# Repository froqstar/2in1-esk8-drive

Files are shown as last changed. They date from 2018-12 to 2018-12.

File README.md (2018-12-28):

# 2in1-esk8-drive
A parametric 3D design for single-motor, dual driven wheel electric skateboards

## What is this about?

This is a parametric 3D design for a electric skateboard motor mount. 
The feature that sets it apart is that it allows to use one motor to drive two wheels of a skateboard, 
giving it more traction especially in cornering.

The parts generated by the OpenSCAD script are shown below:
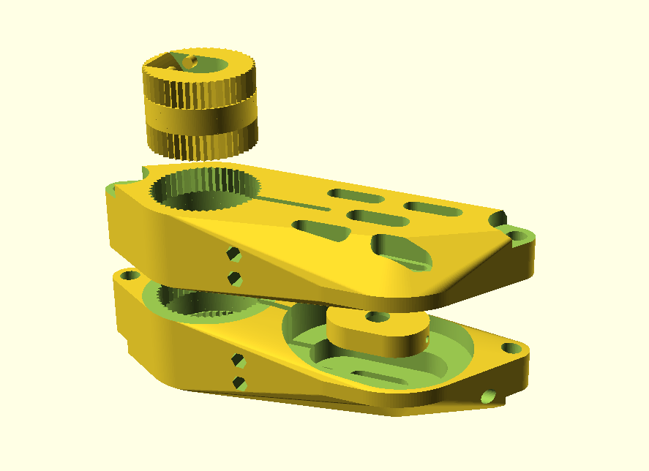
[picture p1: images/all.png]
The whole thing


## Features

- Dual wheel drive with one brushless DC motor/ESC
- Completely parametric, adjustable to your existing hardware
- Vibration-dampened (the parts touching the truck are expected to be printed in TPU)
- Variable mount-to-truck angle
- Belt-tensioning via setscrew

## How do I make this work for my board?

As the design is parametric, almost all parameters can be adjusted according to your setup.
This includes truck and motor dimensions, as well as the type and length of belt used, the number of teeth on your 
pulleys, the diameters of your screws and how sturdy you want the design to be. So just about everything.

The only thing probably requiring some work on your side is the TPU adapter to make it fit to your truck.
Due to the plethora of truck shapes out there and me only having my single board, 
I couldn't model them myself. By default, an adapter for Globe Slant Reverse Kingpin Trucks is included.
Take the output of `truckAdapterBase()` as a base for your own truck adapter.

## Hardware BOM

- A suitable BLDC motor (The current script has the values for a Turnigy Aerodrive SK3 6474 motor)
- Mounting screws for the motor (should be included)
- Two drive belts (HTD5M or similar, 12mm width or more recommended)
- Two wheel & two motor pulleys, fitting your belts.
- A new axle for your motor! As most motors don't support pulleys on both sides, you'll likely need to replace the motor axle with a longer one that protrudes from both ends of the motor. I made one myself.
- 4 screws and locknuts of suitable length and strength (e.g. M3 40mm) to fasten the big parts around the TPU parts.
- 1 screw and locknut to adjust the belt tension on the non-supported motor side. M3 is fine, length depends on the rest of your hardware/parameters.
- 1 bearing for the motor axle. If your motor axle is 8mm in diameter, a standard 608 skateboard bearing is fine.
- Two pieces of threaded rod (e.g. M8) as long as your truck axle is wide, with 8 matching nuts (preferably locknuts) to adjust the distance between the two sides of the mount.  

## Assembly

### Printing the parts
Once you have put in your measurements, all you need to do is open the supplied .scad file with OpenSCAD, generate the STL files and print them.
All parts are expected to be printed in PETG or similar (PLA is not recommended due to it being brittle and having low tolerance for motor heat), except for the truck adapter (the round thing), which is expected to be printed in TPU to make it pressure-fit tightly on the truck and offer vibration dampening for the whole assembly.
Print one of each PETG part, and two TPU truck adapters.

### Steps

1. Slip the truck adapters on your truck.
2. Loosely attach the motor to the mount through the 4 mounting holes.
3. Put in the screws and nuts that are used to fasten the mount around the adapters. Don't tighten them yet, or you won't be able to attach the parts to the truck!
4. Slip the motor mount over the truck adapter in the desired angle and make sure the mount doesn't touch your board when cornering.
5. Put the motor axle bearing in the bearing sleigh, and insert the locknut in the slot. Then, put the bearing sleigh into the cavity in the mount part, bearing-first and with the locknut facing the hole for the tensioning screw. Screw the tensioning screw into the nut.
6. Slip the mount on the other truck adapter on the truck and fit the motor axle in the bearing.
7. Put the threaded rods through the holes at the front and the back parts of the mount, making sure not to forget to put on the two nuts in the middle.
8. Adjust the distance between the mounts.
9. Fasten the mounts around the truck adapters by tightening the four screws.
10. Put on your pulleys, wheels and belts and tension accordingly.
11. Profit :)

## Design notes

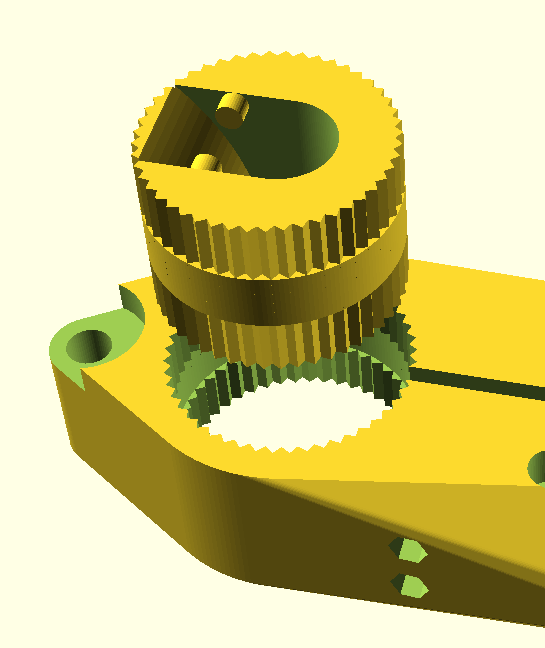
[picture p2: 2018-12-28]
images/adapter.png

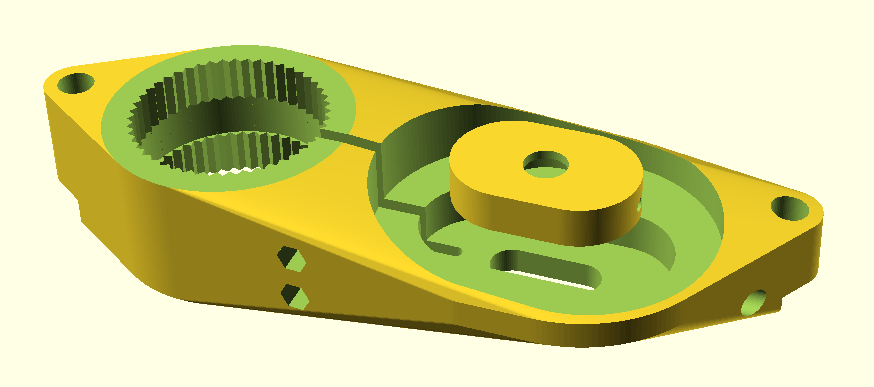
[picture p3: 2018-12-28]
images/bearing.png

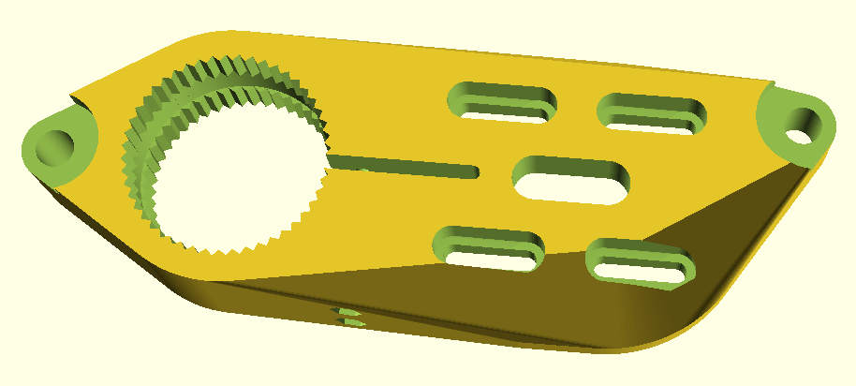
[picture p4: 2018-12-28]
images/motor.png

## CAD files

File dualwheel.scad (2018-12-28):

$fa=2;
$fs=0.4;

PI = 3.14159;

//all values are in mm


// Truck parameters
useableTruckSize = 154; // The distance between the wheels (measured from rubber to rubber, NOT bearing to bearing!)
truckWidth = 18;
truckAdapterDiameter = 42; // You may need to increase this when you have a very thick truck
truckAdapterPlay = 1.3;
truckAdapterAdjustmentAngle = 7.5; // stepsize of mount-to-truck angle adjustment. Has to be a clean divisor of 90°. Smaller steps are harder to print/have less strength!
truckAdapterTensioningSlotWidth = 3; 
truckAdapterTensioningSlotLength = 30;
truckAdapterTensioningScrewDiameter = 3.1;
truckAdapterTensioningScrewLength = 30;
truckAdapterTensioningScrewCount = 2;
truckAdapterTensioningScrewHeadDiameter = 6.1;
truckAdapterTensioningScrewNutDiameter = 5.7;

distanceScrewDiameter = 8; // The screws used to keep the two mounts at constant distance, at motor & axis

// Transmission parameters
beltWidth = 15;
beltLength = 280;
motorPulleyTeeth = 15;
wheelPulleyTeeth = 40;
wheelPulleyWidth = 19;
beltPitch = 5;

motorPulleyCircumference = motorPulleyTeeth * beltPitch;
wheelPulleyCircumference = wheelPulleyTeeth * beltPitch;

// Motor parameters
// SK3 6374 values: http://www.electric-skateboard.builders/uploads/db1493/original/3X/c/4/c40213f09c3a9efb59e033c84dde2ed19bf27e4f.png
motorHousingDiameter = 59; //59
motorHousingDepth = 84.5;
motorClearing = 2;
motorAxisDiameter = 8;
motorAxisClearing = 0.7;
motorClipDiameter = 15;
motorClipDepth = 2;
motorScrewHoleCount = 4;
motorScrewHoleDiameter = 4.4;
motorScrewHoleSpacing = 44;
motorScrewHoleTensioningSpan = 15;
motorScrewHeadDiameter = 8;

// Motor axis bearing parameters
bearingDiameter = 22.1;
bearingDepth = 7;
bearingWallWidth = 2;
bearingScrewDiameter = 3;
bearingScrewNutDiameter = 5.7;
bearingScrewNutHeight = 4.4;
bearingScrewHeadDiameter = 6;

// General structural parameters
truckMountWidth = 30; // width of the truck side of the mount
motorMountWidth = (useableTruckSize - 2 - wheelPulleyWidth*2 - motorHousingDepth) / 2; // width of the motor side of the mount
wallWidth = 6; // the minimum wall width of parts

// The distance between the wheel axis and the motor axis (midpoints).
// Yes, this is incorrect, but that is what the tensioning holes are for ;)
axesDistance = (beltLength - motorPulleyCircumference/2 - wheelPulleyCircumference/2) / 2;


module motorMount() {
	difference() {
		//create outer hull
		mountHullWithAxisHole(false);
		
		//motor clip clearing
		hull() {
			translate([axesDistance - motorScrewHoleTensioningSpan/2, 0, motorMountWidth - motorClipDepth]) {
				cylinder(h=motorClipDepth, d = motorClipDiameter);
			}
			translate([axesDistance + motorScrewHoleTensioningSpan/2, 0, motorMountWidth - motorClipDepth]) {
				cylinder(h=motorClipDepth, d = motorClipDiameter);
			}
		}
		
		//motor mount holes
		for (i = [0:motorScrewHoleCount]) {
			hull() {
				translate([axesDistance - motorScrewHoleTensioningSpan/2, 0, 0]) {
					motorMountingHole(i);
				}
				translate([axesDistance + motorScrewHoleTensioningSpan/2, 0, 0]) {
					motorMountingHole(i);
				}
			}
			hull() {
				translate([axesDistance - motorScrewHoleTensioningSpan/2, 0, -0.5]) { //do a slight slope for the screw head to keep it from sliding inwards
					motorMountingScrewHead(i);
				}
				translate([axesDistance + motorScrewHoleTensioningSpan/2, 0, 0]) {
					motorMountingScrewHead(i);
				}
			}
		}
	}
}

module bearingMount() {
	difference() {
		//create outer hull
		mountHullWithAxisHole(true);
		
		//pocket for bearing sleigh
		translate([axesDistance, 0, motorMountWidth - bearingDepth - bearingWallWidth]) {
			hull() {
				translate([-motorScrewHoleTensioningSpan/2, 0, 0]) {
					bearingSleigh();
				}
				translate([+motorScrewHoleTensioningSpan/2, 0, 0]) {
					bearingSleigh();
				}
			}
			//setscrew
			translate([bearingDiameter/2, 0, bearingDepth/2]) {
				rotate([0,90,0]) {
					cylinder(h=bearingWallWidth + wallWidth + 30, d=bearingScrewDiameter);
				}
			}
			//setscrew head hole
			translate([motorScrewHoleTensioningSpan/2 + bearingDiameter + wallWidth, 0, bearingDepth/2]) {
				rotate([0,90,0]) {
					cylinder(h=wallWidth + 30, d=bearingScrewHeadDiameter);
				}
			}
		}
	}
}


module mountHullWithAxisHole(isLeft = false) {
	difference() {
		//outer shape
		hull() {
			cylinder(h=truckMountWidth, r=truckAdapterDiameter/2 + wallWidth);
			
			translate([axesDistance - motorScrewHoleTensioningSpan/2, 0, 0]) {
				hull() {
					cylinder(h=wallWidth, r=motorPulleyCircumference/(2*PI) + 2);
					translate([0,0,motorMountWidth]) {
						cylinder(h=wallWidth, r=motorHousingDiameter/2 + motorClearing);
					}
				}
			}
			translate([axesDistance + motorScrewHoleTensioningSpan/2, 0, 0]) {
				hull() {
					cylinder(h=wallWidth, r=motorPulleyCircumference/(2*PI) + 2);
					translate([0,0,motorMountWidth]) {
						cylinder(h=wallWidth, r=motorHousingDiameter/2 + motorClearing);
					}
				}
			}
			// rear distance screw mount
			translate([-(truckAdapterDiameter/2+wallWidth*2+distanceScrewDiameter/2), 0, 0]) {
				cylinder(h=truckMountWidth, d=distanceScrewDiameter+wallWidth);
			}
			// front distance screw mount
			translate([axesDistance + motorHousingDiameter/2 + wallWidth*3, (isLeft ? 1:-1) * (motorHousingDiameter/2 - wallWidth*2), 0]) {
				cylinder(h=motorMountWidth + wallWidth, d=distanceScrewDiameter+wallWidth);
			}
		}
		// rear distance screw hole
		translate([-(truckAdapterDiameter/2+wallWidth*2+distanceScrewDiameter/2), 0, 0]) {
			cylinder(h=truckMountWidth, d=distanceScrewDiameter);
		}
		translate([-(truckAdapterDiameter/2+wallWidth*2+distanceScrewDiameter/2), 0, 0]) {
			cylinder(d=21, h=6);
		}
		// front distance screw hole
		translate([axesDistance + motorHousingDiameter/2 + wallWidth*3, (isLeft ? 1:-1) * (motorHousingDiameter/2 - wallWidth*2), 0]) {
			cylinder(h=truckMountWidth, d=distanceScrewDiameter);
		}
		translate([axesDistance + motorHousingDiameter/2 + wallWidth*3, (isLeft ? 1:-1) * (motorHousingDiameter/2 - wallWidth*2), 0]) {
			cylinder(d=21, h=6);
		}
		
		//axis hole
		hull() {
			translate([axesDistance - motorScrewHoleTensioningSpan/2, 0, 0]) {
				cylinder(h=motorMountWidth, r = motorAxisDiameter/2 + motorAxisClearing);
			}
			translate([axesDistance + motorScrewHoleTensioningSpan/2, 0, 0]) {
				cylinder(h=motorMountWidth, r = motorAxisDiameter/2 + motorAxisClearing);
			}
		}
		//plain mount surfaces
		translate([0,0,truckMountWidth]) {
			cylinder(h=motorMountWidth, d=truckAdapterDiameter + 2*wallWidth);
		}
		hull() {
			translate([axesDistance - motorScrewHoleTensioningSpan/2, 0, motorMountWidth]) {
				cylinder(h=motorMountWidth, r = motorHousingDiameter/2);
			}
			translate([axesDistance + motorScrewHoleTensioningSpan/2, 0, motorMountWidth]) {
				cylinder(h=motorMountWidth, r = motorHousingDiameter/2);
			}
		}
		
		truckAdapterBase(truckAdapterDiameter + truckAdapterPlay);
		
		//truck adapter tensioning slot
		hull() {
			cylinder(h=truckMountWidth, d=truckAdapterTensioningSlotWidth);
			translate([truckAdapterDiameter/2 + truckAdapterTensioningSlotLength,0,0]) {
				cylinder(h=truckMountWidth, d=truckAdapterTensioningSlotWidth);
			}
		}
		//truck adapter tensioner screwholes
		for (i = [0:truckAdapterTensioningScrewCount-1]) {
			truckSlotTensioningScrewHole(i, isLeft);
		}
	}
}


module motorMountingHole(number) {
	rotate([0,0,360/motorScrewHoleCount*number + (360/motorScrewHoleCount)/2]) {
		translate([motorScrewHoleSpacing/2,0,0]) {
			cylinder(h=motorMountWidth, d=motorScrewHoleDiameter);
		}
	}
}

module motorMountingScrewHead(number) {
	rotate([0,0,360/motorScrewHoleCount*number + (360/motorScrewHoleCount)/2]) {
		translate([motorScrewHoleSpacing/2,0,0]) {
			cylinder(h=motorMountWidth-wallWidth, d=motorScrewHeadDiameter);
		}
	}
}

module truckSlotTensioningScrewHole(number, isLeft=false) {
	
	translate([	truckAdapterDiameter/2 + wallWidth, 0, (truckMountWidth/(truckAdapterTensioningScrewCount+1)) * (number + 1)]) {
		rotate([(isLeft ? -1:1)*90,0,0]) {
			cylinder(h=motorHousingDiameter + 2*wallWidth,d=truckAdapterTensioningScrewDiameter, center=true);
			//head hole
			translate([0,0,truckAdapterTensioningScrewLength]) {
				cylinder(h=truckAdapterDiameter, d=truckAdapterTensioningScrewHeadDiameter, center=true);
			}
			//nut hole
			translate([0,0,-truckAdapterTensioningScrewLength+4]) {
				nutM3(h=30);
				//cube([truckAdapterTensioningScrewNutDiameter, truckAdapterTensioningScrewNutDiameter *1.4, 30], center=true);
			}
		}
	}
}
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

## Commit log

2018-12-27 added initial dualwheel scad file
    [dualwheel.scad]
2018-12-27 documentation & cleanup
    [dualwheel.scad]
2018-12-28 added front distance screw mount
    [dualwheel.scad]
2018-12-28 add screenshot folder
    [dualwheel.scad]
2018-12-28 added BOM & assembly steps
